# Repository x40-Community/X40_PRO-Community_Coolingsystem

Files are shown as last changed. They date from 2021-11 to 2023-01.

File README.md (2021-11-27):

# X40-Community Coolingsystem
The X40 community cooling system replaces the ailing part cooling system from Weedo. In particular, materials that require a lot of cooling are printed much better.

For more informations see: http://www.x40-community.org/index.php/the-3d-printer/weedo-x40-coolingsystem

## Please make sure to use the Extrudr GreenTec Pro material when printing the hotend cover. Other materials are unsuitable and cannot take the heat! 



## The X40 Community Coolingsystem has the following advantages:

   - Higher volume throughput due to larger fans
   - Due to the stronger cooling capacity, some materials can also be printed faster
   - The fan seems to be more controllable, especially at low speeds
   - The air outlet opening is closer to the nozzle
   - The ventilation duct is very stable and does not break off immediately if warping occurs
   - The Hotend Cover can easily be dismantled e.g. to change the nozzle
   - The fan can easily be exchangen
   - Hotend cover can easily be printed by yourself (see cloud for instructions)
   - Further improvements cannot be ruled out ;-)



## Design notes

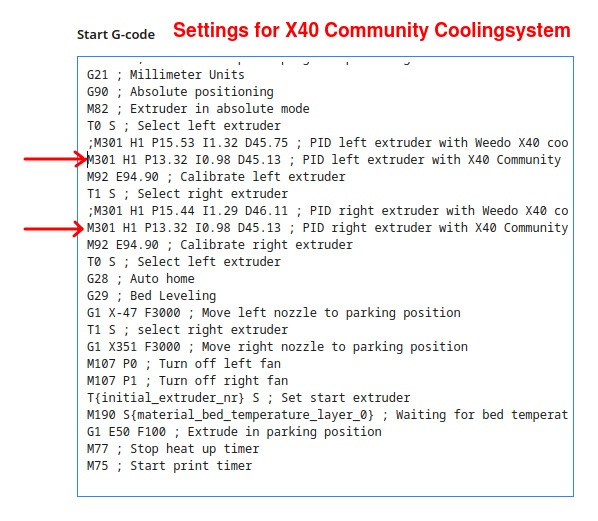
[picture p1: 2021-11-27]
cura_startcode.jpg

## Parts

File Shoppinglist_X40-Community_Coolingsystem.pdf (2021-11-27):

Tabelle1

## Shoppinglist for X40-Community Collingsystem

Position | Quantity | Name | Manufacturer | Supplier
1 | 2 Hotend Cover | | DIY | Material: Extrudur GreenTEC Pro, black (https://www.3djake.de/extrudr/green-tec-pro-schwarz)
2 | 2 Blower fan 4020 – 24V DC | | WINSINN | Amazon (https://www.amazon.de/WINSINN-Gebl%C3%A4seventilator-b%C3%BCrstenlos-3D-Drucker-Extruder/dp/B07L2XZKS7)
3 | 2 MK8 Silicone shoe | | | Amazon (https://www.amazon.de/SOOWAY-Aluminium-Abdeckung-Best%C3%A4ndig-Temperatur/dp/B07GB6Y93W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)
4 | 2 JST-XH (2,54mm) Female/Male Extrension cable 600mm | | DIY | Bohrers (https://shop.bohrers.de/jst-xh-stecker-satz-2pin.html)
5 | 6 Cylinder head screw ISO 4762-M3x18-A2 | | - | Online Schrauben (https://online-schrauben.de/shop/Schrauben/Innensechskantschrauben/ISO-4762-DIN-912-Zylinderkopfschrauben-mit-Innensechskant-aehnl.-DIN-912/Edelstahl-Rostfrei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)
6 | 6 Nut DIN 934-M3-A2 or Nut ISO 4032-M3-A2 | | - | Online Schrauben (https://online-schrauben.de/shop/Muttern/Sechskantmuttern/DIN-934-Sechskantmuttern-aehnl.-ISO-4032/Edelstahl-Rostfrei-A2)

It is difficult to make the extension cable yourself. If you can find someone who can do this for you, Then I would have it done. The cables must be connected crosswise!

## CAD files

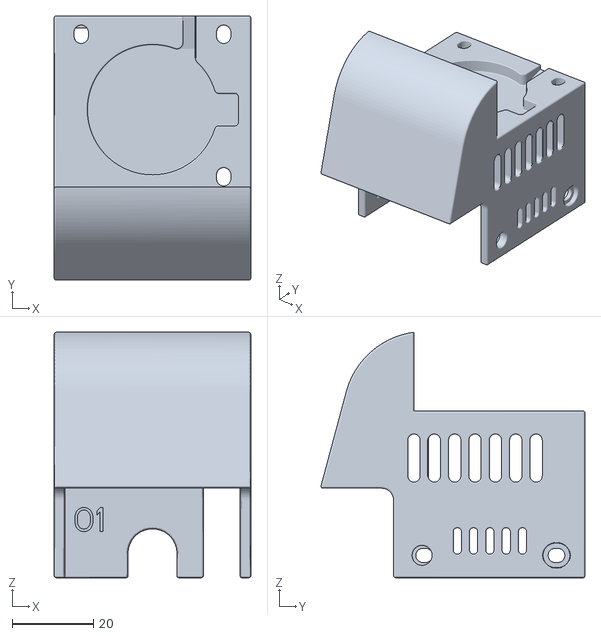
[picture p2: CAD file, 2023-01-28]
xxx-2550_hotend_cover-01.stl
48.3 x 64.8 x 60.3

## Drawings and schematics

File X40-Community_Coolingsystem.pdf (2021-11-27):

# X40 Community Coolingsystem

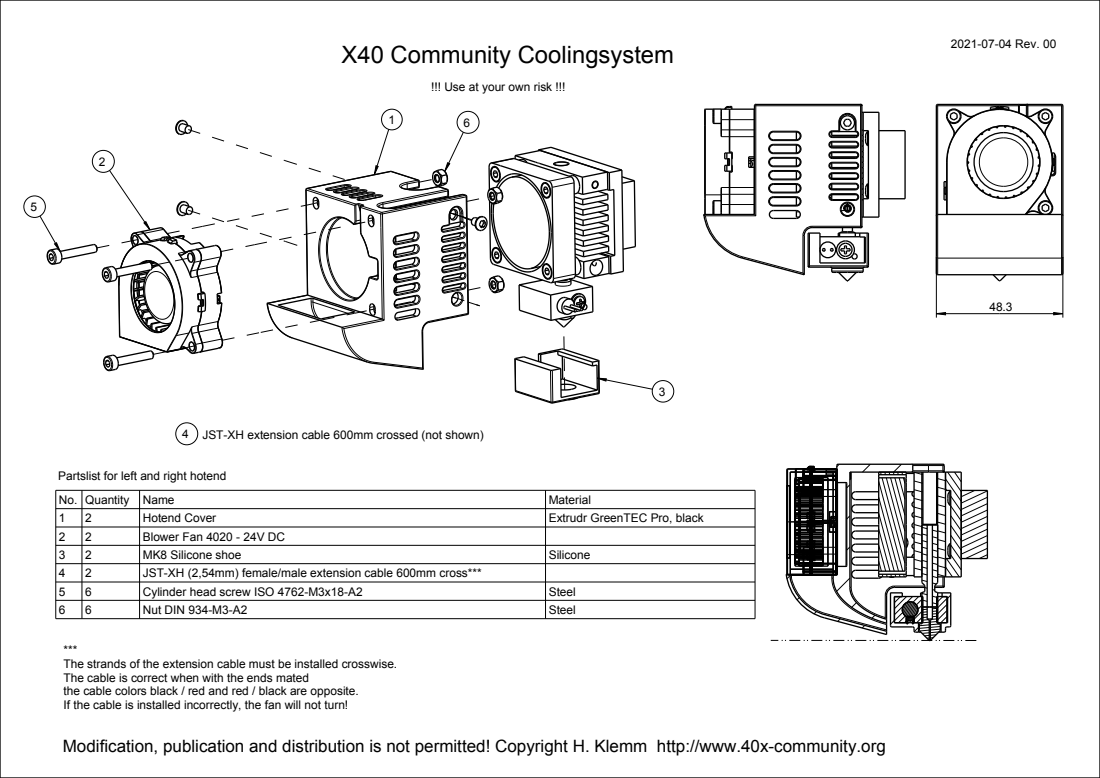
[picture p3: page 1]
No. Quantity Name; Material; Hotend Cover; Extrudr GreenTEC Pro, black; Blower Fan 4020 - 24V DC; MK8 Silicone shoe; Silicone; JST-XH (2,54mm) female/male extension cable 600mm cross***; Cylinder head screw ISO 4762-M3x18-A2; Steel; Nut DIN 934-M3-A2; 2021-07-04 Rev. 00

!!! Use at your own risk !!!

4 JST-XH extension cable 600mm crossed (not shown)

Partslist for left and right hotend

The strands of the extension cable must be installed crosswise.
The cable is correct when with the ends mated
the cable colors black / red and red / black are opposite.
If the cable is installed incorrectly, the fan will not turn!
Modification, publication and distribution is not permitted! Copyright H. Klemm http://www.40x-community.org

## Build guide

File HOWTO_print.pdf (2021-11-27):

# HOWTO PRINT

X40-Community.org

- Open the SLT-file from the hotend cover with Cura.
- Rotate the object so that the top rests on the build plate.

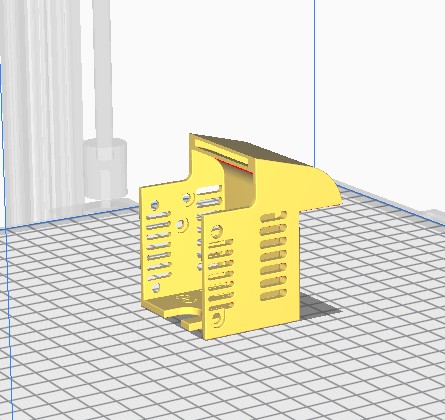
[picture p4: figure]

- Select the material Extrudr GreenTEC Pro Black for the left nozzle and deactivate the right nozzle.
- Select the Visual Fine print profile.
- Activate “Check all” in the Cura preferences

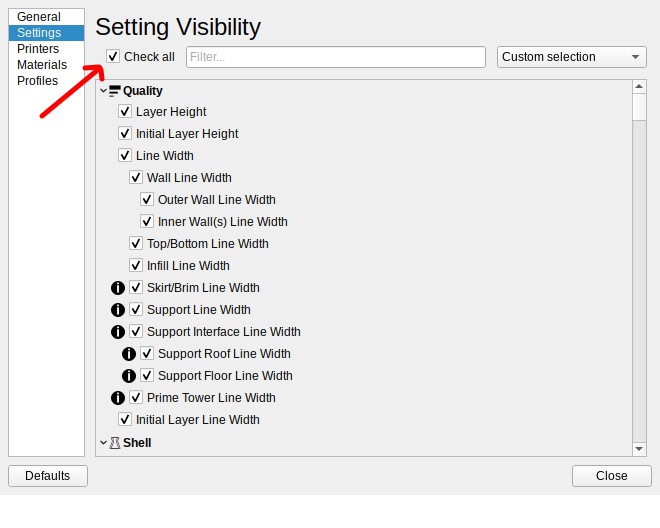
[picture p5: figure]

- Change the infill line distance to 3mm

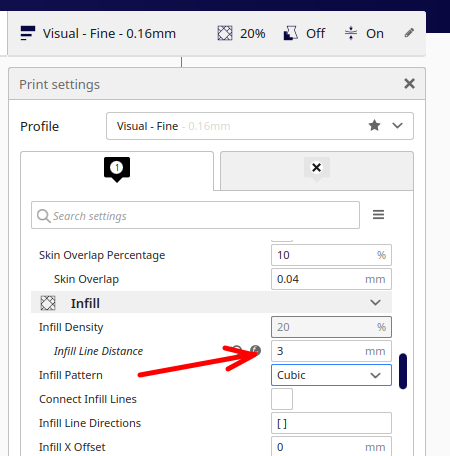
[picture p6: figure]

- Activate support and switch support placement to Touching Buildplate

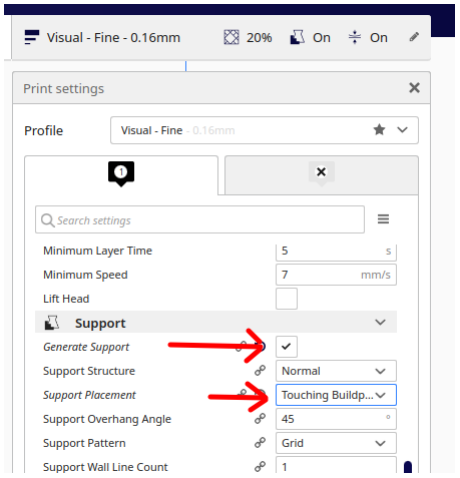
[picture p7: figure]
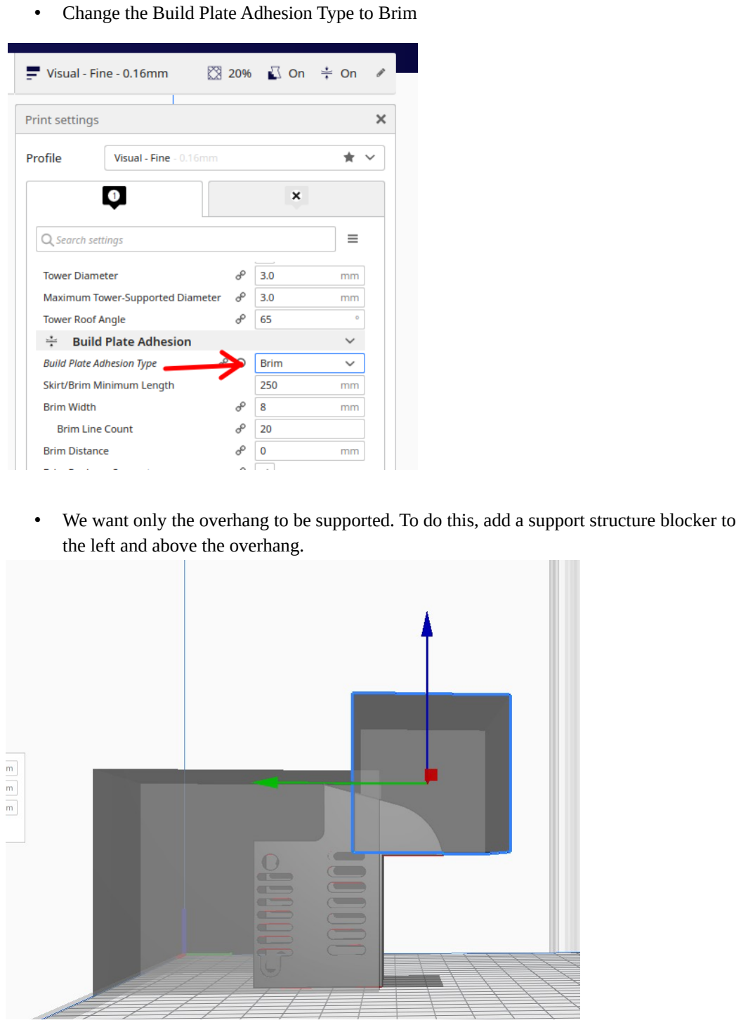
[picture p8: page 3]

- Change the Build Plate Adhesion Type to Brim
- We want only the overhang to be supported. To do this, add a support structure blocker to the left and above the overhang.

- After slicing, the preview should look like this...

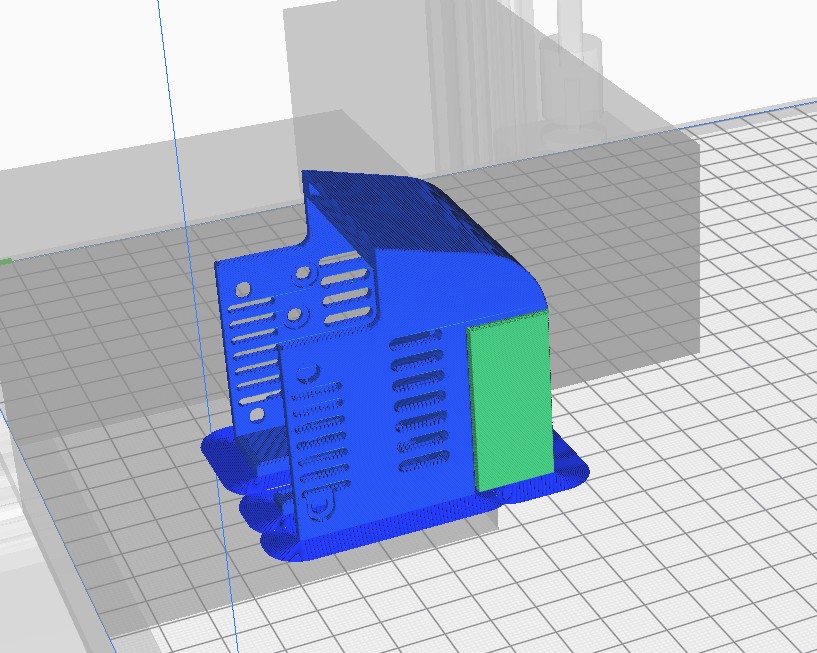
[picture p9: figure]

- After removing the support structure, the sealing surface to the fan should be smoothed with a file or sandpaper on the edge of the table so that there is no gap between the fan and the cover. The fan can be adjusted accordingly through the elongated holes.

Happy printing

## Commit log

2021-11-27 Add X40 Community Coolingsystem Rev. 00
    [hotend_cover-00.stl]
2023-01-28 Add upgrade to hotend cover Rev. 01
    [hotend_cover-00.stl, xxx-2550_hotend_cover-01.stl]
